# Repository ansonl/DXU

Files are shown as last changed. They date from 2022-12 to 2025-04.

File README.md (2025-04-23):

# DXU - Dual Extrusion Upgrade for Ultimaker Original+ and Ultimaker 2+

## Table of Contents

- ### [Marlin 2 firmware, calibration, and configuration instructions for DXUv2](https://github.com/ansonl/DXU/blob/master/Firmware/README.md) 

- ### [DXUv2 3D printable files](https://github.com/ansonl/DXU/tree/master/AL-DXUv2)

  - DXUv2 reuses the stock Ultimaker printhead metal parts for a more compact and durable printhead.

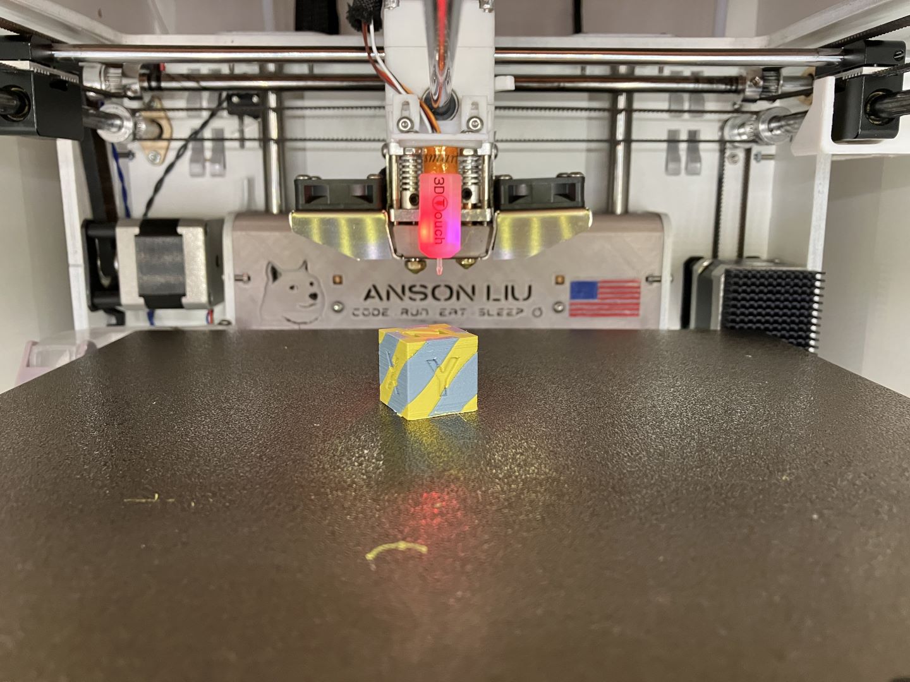
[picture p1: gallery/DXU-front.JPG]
DXU front


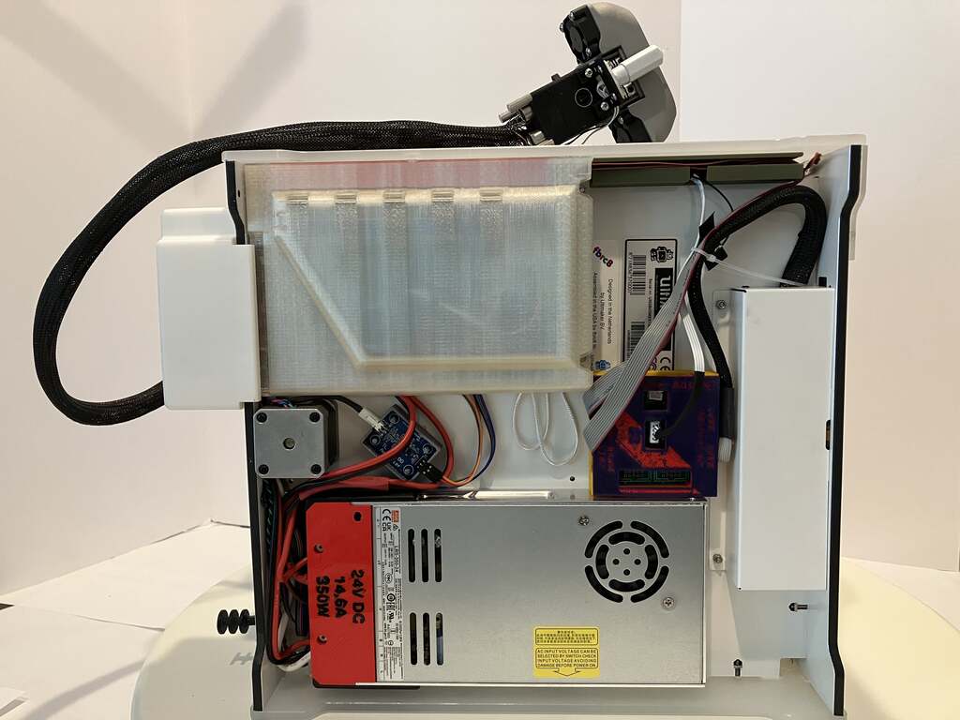
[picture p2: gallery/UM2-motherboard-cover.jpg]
DXUv2 bottom


### Improved/Updated DXU resources are in the `AL-*` folders. 

## DXUv2

1. See [post1](https://community.ultimaker.com/topic/24553-dxu-efficient-dual-extrusion-upgrade-for-um2/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) and [post2](https://community.ultimaker.com/topic/24553-dxu-efficient-dual-extrusion-upgrade-for-um2/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) for DXUv2 info
1. Make all the parts in `AL-DXUv2/master parts to print/` out of high temperature plastic like SLS Nylon.
1. Make the 3 hotend holder models in `AL-DXUv2/prototyping parts/DXUv2-hotend-holder` out of aluminum. You can machine it out of the existing Ultimaker part or get it SLM printed in aluminum. I did both and the SLM printed part from UnionFab is much more precise. Have the factory use my specification PDF for the threading depths and locations. This is save you a lot of crying and pain trying to thread blind holes yourself.

## Original DXU

1. [Marlin 2 firmware for DXU](https://github.com/ansonl/Marlin-DXU)
2. Dock adapted for UMO+ frame
3. Heater clamps with 1mm thin jaws. The linked Taobao seller sells a quality all metal hotend but the heatsink flanges are only 1mm vs 2mm apart. The seller says he can do a special order of heatsinks with 2mm flange spacing with a minimum order quantity of 50. 
4. Cura profile with calibration and improvements for DXU UMO+ are merged into Cura. 
5. Input Shaping calibration gcode and presets.

## Cura profile notes

I have not had time to update all the downloadable Cura profiles with the [better adaptive start/end gcode](https://ansonliu.com/2024/10/cura-adaptive-dual-extruder-start-gcode/) located in `AL-DXUv2/start-end-gcode`. Please copy and paste them into your Cura printer settings to use them.

### DISCUSSION:
https://community.ultimaker.com/topic/24553-dxu-another-dual-extrusion-upgrade-for-um2/

### CREDITS:

##### DXU:  
Original DXU by yyh1002

DXU variant by benleo888
##### Hardware:  
Lever action is inspired by Ultimaker 3.   
##### Firmware:   
Marlin 2 firmware

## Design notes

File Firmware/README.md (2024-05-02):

## Marlin 2 Configurations
Configurations for UMO+, UM2, UM2+ merged upstream to MarlinFirmware/Configurations are available at: [MarlinFirmware/Configurations](https://github.com/MarlinFirmware/Configurations/tree/bugfix-2.1.x/config/examples/Ultimaker)

These configurations are automatically merged with Configuration file version updates so accuracy is not guaranteed. All configurations can be used on single extruder printers by changing the extruder count from 2 to 1 and commenting out the multi extruder, thermistor, and extruder defines.

### PID Values Calibration

Determine your own PID by running [M303](https://marlinfw.org/docs/gcode/M303.html) or use the below values as reference.

#### Hotend PID values using 35 W heater cartridge

| Printhead | PID values in Gcode. Save to EEPROM with `M500` |
| --- | --- |
| Stock UM2+ | `M301 P8.86 I0.68 D28.86` |
| DXU PTFE with PI spacer | `M301 P13.95 I1.77 D27.42` |
| DXU all-metal | `M301 P10.85 I1.08 D27.33` |
| DXUv2 non-lifting nozzle (left) | `M301 E0 P15.15 I1.78 D32.26` |
| DXUv2 lifting nozzle (left) | `M301 E1 P15.53 I1.79 D33.71` |

#### Heated bed PID values using Ultimaker 120 W heated bed

| Printhead | PID values in Gcode. Save to EEPROM with `M500` |
| --- | --- |
| Stock UM glass bed | `M304 P124.55 I23.46 D165.29` |
| Textured PEI on magnetic metal sheet | `M304 D372.47 I14.05 P88.61` |

### EStep (steps/mm) Calibration

Determine your extruder steps/mm to avoid over/under extrusion. Even stock and clone extruders have variances that deviate from default steps/mm values!

| Extruder | steps/mm with 1.8°/step (UMO+/UM2+ extruder motor) | steps/mm with 0.9°/step (UM2 extruder motor) |
| --- | --- | --- |
| UM2+ Extruder | `M92 E369` | `M92 E738` |
| UM2+ Extruder (aliexpress) | `M92 E357` - `M92 E360` | `M92 E715` - `M92 E720` |

1. Disconnect bowden tube and printhead from extruder. 
2. Disable Cold Extrude protection. `M302 P1`
3. Set current extruder position in software to 0. `G92 E0`
4. Feed filament into extruder. Mark the location on the filament that sticks out from the extruder filament output hole using a sharpie. 
5. Move 100 mm of filament forward. `G0 E100 F100`
6. Mark location of filament that sticks out from the extruder filament output hole.
7. Measure distance between markings to determine actual distance of filament moved forward.
8. Calculate correct steps/mm manually or `corrected esteps = current esteps * (actual distance in mm)/100mm` or use [TH3D EStep Calculator](https://www.th3dstudio.com/estep-calculator/)
9. Set new steps/mm `M92 E<esteps>` e.g. `M92 E369`.
10. Return to step 3 and verify 100m of filament is actually moved.

### Hotend Offset Calibration

Stock hotend offset values for the second extruder are `M218 T1 X18 Y0 Z-2`
Stock probe offset values are `NOZZLE_TO_PROBE_OFFSET { 9, -19.5, -1 }`

#### Hotend Offset X/Y Calibration

1. Print dual X/Y calibration print [here](https://www.thingiverse.com/thing:1741265) or in the `AL-Hotend Calibration folder`.
2. Compare print results and set hotend offsets with [`M218`](https://marlinfw.org/docs/gcode/M218.html). `M218 T1 XNNN YNNN`

#### Hotend Offset Z Calibration

1. Switch to first extruder. `T0`
2. Home Z axis. Optionally home X/Y axis and move printhead to center of X/Y. `G28` `G0 X100 Y100`
3. Move Z axis to `0` position where nozzle touches or is ~0.1 mm above the bed for the paper calibration method. Using a piece of paper/gauge sliding between nozzle and bed, note the physical distance (not the value on the screen) between the nozzle and bed at Z0. `G0 Z0`
4. Move Z axis down at least `5 mm` to make space for the second extruder. `G0 Z5`
5. Manually activate second extruder with your hand or a tool. Do not activate with toolchange gcode `T1` unless the `HOTEND_OFFSET_Z` for the second extruder is set to `0`.
6. Move Z axis up until the physical distance between the second nozzle and bed are the same as the physical distance between the first nozzle and bed that you remembered earlier. Use a paper/gauge to get the right distance. Use the negative values of the Z position reported by the printer software as the `HOTEND_OFFSET_Z` for the second extruder. E.g. If the reported Z position is 2.5 mm, use -2.5 mm. 
7. Set new hotend Z offset with `M218`. `M218 T1 ZNNNN`

### Toolchange G-code

The movement commands to switch between the extruders can be set in firmware or the slicer. I recommend setting this in firmware rather than in the slicer. This way the toolchange action and offset compensation is completely handled by firmware and you do not need to remember to set up the special movements and offsets in every slicer you use (if the slicer even has support for it). When the toolchange is set in the firmware, all that is needed to change a tool is calling `TXX` where `XX` is the new extruder index starting from `0`. 

Configuration macros to change in Marlin are `EVENT_GCODE_TOOLCHANGE_T0` and `EVENT_GCODE_TOOLCHANGE_T1`. All movements are based off of hotend 0's offset which should be `0,0,0`. Otherwise there would be no way to know which hotend offset is being switched from if there are more than 2 hotends. Marlin will translate the movement by the current hotend offset. 

| Printer Case | Extruder | Toolchange G-code |
| --- | --- | --- |
| UM2/UM2+ | `T0` | `G90\nG0 X214 F7200\nG0 Y178\nG0 X219 F1800\nG0 Y194.5\nG0 X214\nG0 Y169 F7200` |
| UM2/UM2+ | `T1` | `G90\nG0 X214 F7200\nG0 Y209\nG0 X220 F1800\nG0 Y193\nG0 X214\nG0 Y169 F7200` |
| UMO+ | `T0` | `G90\nG0 X211 F7200\nG0 Y167\nG0 X217 F1800\nG0 Y182\nG0 X211\nG0 Y166 F7200` |
| UMO+ | `T1` | `G90\nG0 X211 F7200\nG0 Y198\nG0 X219 F1800\nG0 Y181\nG0 X211\nG0 Y166 F7200` |

### Save Printer Settings

Save settings to persistent storage on board the printer EEPROM with `M500`

## Marlin 2 Firmware 
Firmware source code customized for 3D printers

| Machine style | Motherboard (controller board) | Firmware source code branch |
| --- | --- | --- |
| UMO+/UM2/UM2+ w/ DXU | `ULTIMAINBOARD` | [ansonl/Marlin:dxu-ultimaker-ultimainboard-2](https://github.com/ansonl/Marlin/tree/dxu-ultimaker-ultimainboard-2) |
| UMO+/UM2/UM2+ w/ DXU | `BTT_OCTOPUS_PRO_V1_0` | [ansonl/Marlin:dxu-ultimaker-btt-octopus-pro-1](https://github.com/ansonl/Marlin/tree/dxu-ultimaker-btt-octopus-pro-1) |

*If you have a modified Marlin 2 firmware that you would like to add to this list, please add it in a PR.*

### Firmware notes for each branch versus *MarlinFirmware/Marlin* upstream 

#### ansonl/Marlin:dxu-ultimaker-ultimainboard-2
- https://github.com/MarlinFirmware/Marlin/issues/25117 - Marlin 2.1.2 Input Shaping may skip steps on AVR at high speeds > 250mm/s.

#### ansonl/Marlin:dxu-ultimaker-btt-octopus-pro-1
- Pins changes
  - `pins_BTT_OCTOPUS_PRO_V1_0.h`
  - `pins_BTT_OCTOPUS_V1_common.h`
- https://github.com/MarlinFirmware/Marlin/pull/25683 - OTA Firmware update via SDIO card update

### Merged to upstream
- https://github.com/MarlinFirmware/Marlin/pull/23466
- https://github.com/MarlinFirmware/Marlin/pull/24553
- https://github.com/MarlinFirmware/Marlin/pull/24797
- https://github.com/MarlinFirmware/Marlin/pull/25399
- https://github.com/MarlinFirmware/Marlin/pull/25707

## Cura printer settings

```json
"overrides":
    {
        "line_width": { "value": "machine_nozzle_size" },
        "machine_depth": { "default_value": 216 },
        "machine_disallowed_areas":
        {
            "default_value": [
                [
                    [100, -102.5],
                    [110, -102.5],
                    [110, -62.5],
                    [100, -62.5]
                ]
            ]
        },
        "machine_end_gcode": { "value": "\"\"  if machine_gcode_flavor == \"UltiGCode\" else \"G91 ;Relative movement\\nG0 X-8.0 Y-8.0 Z3.5 E-4.5 F18000 ;Wiping+material retraction ;increase bed lower 0.5>5.0 and add Y movement\\nG0 F10000 Z1.5 E4.5 ;Compensation for the retraction\\nG90 ;Disable relative movement\\nM400 ;wait for all moves in planner to complete\\nG90 ;absolute positioning\\nM104 S0 T0 ;extruder heater off\\nM104 S0 T1\\nM140 S0 ;turn off bed\\nT0 ; move to the first head\\nG27; park toolhead\\nM107 ;fan off\\nM355 S0;turn off case light\"" },
        "machine_extruder_count": { "default_value": 1 },
        "machine_gcode_flavor": { "default_value": "RepRap (Marlin/Sprinter)" },
        "machine_head_with_fans_polygon":
        {
            "default_value": [
                [-46, 30],
                [-46, -34],
                [66, 30],
                [66, -34]
            ]
        },
        "machine_heat_zone_length": { "default_value": 20 },
        "machine_heated_bed": { "default_value": true },
        "machine_height": { "default_value": 208 },
        "machine_max_feedrate_x": { "default_value": 300 },
        "machine_max_feedrate_y": { "default_value": 300 },
        "machine_max_feedrate_z": { "default_value": 40 },
        "machine_min_cool_heat_time_window": { "default_value": 15.0 },
        "machine_name": { "default_value": "dxu2" },
        "machine_nozzle_cool_down_speed": { "default_value": 0.8 },
        "machine_nozzle_expansion_angle": { "default_value": 45 },
        "machine_nozzle_head_distance": { "default_value": 3 },
        "machine_nozzle_heat_up_speed": { "default_value": 1.4 },
        "machine_nozzle_size": { "default_value": 0.4 },
        "machine_start_gcode": { "value": "\"\"  if machine_gcode_flavor == \"UltiGCode\" else \"; DXUv2 improved start priming Gcode for dual nozzles for single material print by ansonl\\nM355 S1 P25 ; Turn on case light dim\\nM190 S{material_bed_temperature_layer_0}\\nG28 ; Home all\\nG29 ; Run automatic bed leveling. Comment this line out if auto bed leveling is not desired.\\nM104 T0 S{material_standby_temperature, 0} ; Preheat T0 to standby temp\\nG21 ; Metric values\\nG90 ; Absolute positioning\\nM82 ; Set extruder to absolute mode\\nM107 ; Start with the fan off\\nM200 D0 T{initial_extruder_nr} ; Reset filament diameter\\nG0 X200 F7200 ; move to safe X and Y location from right side after ending ABL homing\\nG1 Y150 F7200\\nM104 T{initial_extruder_nr} S{material_print_temperature_layer_0, initial_extruder_nr}\\nT{initial_extruder_nr} ;switch to the first nozzle used for print\\nM400 ;finish all moves\\nG0 Z20 F2400\\nG0 X214 F18000\\nG0 Y2 F18000\\nM109 T{initial_extruder_nr} S{material_print_temperature_layer_0, initial_extruder_nr}\\n;Final wipe sequence for initial extruder\\nG0 X212 Z0.3 F600\\nG92 E05\\nG1 Y45 E6.5 F1000\\nG92 E0\\nG1 E-0.5 F1500 ; retract\\nG92 E0\\nG1 Y100 F18000\\n;end of startup sequence\\n\\nM355 S1 P50;turn on case light\"" },
        "machine_use_extruder_offset_to_offset_coords": { "default_value": false },
        "machine_width": { "default_value": 221 },
        "material_adhesion_tendency": { "enabled": true },
        "material_diameter": { "default_value": 1.75 },
        "prime_tower_position_x": { "value": "180" },
        "prime_tower_position_y": { "value": "160" },
        "retraction_amount": { "default_value": 3 },
        "retraction_min_travel": { "value": "line_width * 2" },
        "retraction_speed": { "default_value": 25 },
        "switch_extruder_prime_speed": { "value": "retraction_prime_speed" },
        "switch_extruder_retraction_amount": { "value": "retraction_amount" },
        "switch_extruder_retraction_speed": { "value": "retraction_retract_speed" },
        "switch_extruder_retraction_speeds": { "value": "retraction_speed" },
        "travel_avoid_distance": { "value": "3 if extruders_enabled_count > 1 else machine_nozzle_tip_outer_diameter / 2 * 1.5" }
    }
  ```

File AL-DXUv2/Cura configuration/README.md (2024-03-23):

# Cura Profile Installation

1. Download the latest Cura profile `*.zip` file in this directory.
2. Unzip the archive keeping the files within the respective `definitions`, `extruders`, `variants` folders.
3. Move the folders to the Cura configuration directory `%HOME%/AppData/Roaming/cura/XXX/` where `XXX` is the Cura version number. This will merge the unzipped folders' contents with the existing Cura profile folders' contents.
4. Close and restart Cura.
5. Add the DXUv2 printer as a non-networked printer. DXUv2 printers will be listed under the DXU category.

## Retraction Settings

My optimal retraction settings to use as a starting point. Increasing the nozzle switch retraction distance ensures that no oozing occurs from the inactive extruder. 

| Setting | Value |
| --- | --- |
| Retraction Distance | 2.4 mm |
| Retraction Speed | 25 mm/s |
| Nozzle Switch Retraction Distance | 16 mm |
| Nozzle Switch Retraction Speed | 20 mm/s |

## Start Gcode

Optimized start gcode that properly primes both extruders **regardless of previous nozzle switch retraction state**. The final prime wipes on a previous prime line that helps clear the nozzle of any oozing. 

```
; Octolapse variables
; Script based on an original created by tjjfvi (https://github.com/tjjfvi)
; An up-to-date version of the tjjfvi's original script can be found
; here:  https://csi.t6.fyi/
; Note - This script will only work in Cura V4.2 and above!
; --- Global Settings
; layer_height = {layer_height}
; smooth_spiralized_contours = {smooth_spiralized_contours}
; magic_mesh_surface_mode = {magic_mesh_surface_mode}
; machine_extruder_count = {machine_extruder_count}
; --- Single Extruder Settings
; speed_z_hop = {speed_z_hop}
; retraction_amount = {retraction_amount}
; retraction_hop = {retraction_hop}
; retraction_hop_enabled = {retraction_hop_enabled}
; retraction_enable = {retraction_enable}
; retraction_speed = {retraction_speed}
; retraction_retract_speed = {retraction_retract_speed}
; retraction_prime_speed = {retraction_prime_speed}
; speed_travel = {speed_travel}
; --- Multi-Extruder Settings
; speed_z_hop_0 = {speed_z_hop, 0}
; speed_z_hop_1 = {speed_z_hop, 1}
; retraction_amount_0 = {retraction_amount, 0}
; retraction_amount_1 = {retraction_amount, 1}
; retraction_hop_0 = {retraction_hop, 0}
; retraction_hop_1 = {retraction_hop, 1}
; retraction_hop_enabled_0 = {retraction_hop_enabled, 0}
; retraction_hop_enabled_1 = {retraction_hop_enabled, 1}
; retraction_prime_speed_0 = {retraction_prime_speed, 0}
; retraction_prime_speed_1 = {retraction_prime_speed, 1}
; retraction_retract_speed_0 = {retraction_retract_speed, 0}
; retraction_retract_speed_1 = {retraction_retract_speed, 1}
; retraction_speed_0 = {retraction_speed, 0}
; retraction_speed_1 = {retraction_speed, 1}
; retraction_enable_0 = {retraction_enable, 0}
; retraction_enable_1 = {retraction_enable, 1}
; speed_travel_0 = {speed_travel, 0}
; speed_travel_1 = {speed_travel, 1}
; material_bed_temperature={material_bed_temperature}
; material_print_temperature={material_print_temperature}
; material_print_temperature_layer_0={material_print_temperature_layer_0}
; switch_extruder_retraction_amount_0={switch_extruder_retraction_amount, 0}
; switch_extruder_retraction_amount_1={switch_extruder_retraction_amount, 1}

; DXUv2 improved start priming Gcode for dual nozzles for multi-material print
M355 S1 P25 ; Turn on case light dim
M190 S{material_bed_temperature_layer_0}
G28 ; Home all
;M420 S1 ; Enable and load bed mesh
G29 ; Run automatic bed leveling. Comment this line out if auto bed leveling is not desired.
M104 T0 S{material_standby_temperature, 0} ; Preheat T0 to standby temp
M104 T1 S{material_standby_temperature, 1} ; Preheat T1 to standby temp
G21 ; Metric values
G90 ; Absolute positioning
M82 ; Set extruder to absolute mode
M107 ; Start with the fan off
M200 D0 T0 ; Reset filament diameter
M200 D0 T1 ; Reset filament diameter
G0 X200 F7200 ; Move to safe X and Y location from right side after ending ABL homing. Move X before Y to avoid hitting switching lever.
G1 Y150 F7200
; Prime routine for T1 in normally 
T1 ; move to the nozzle 2
M104 T1 S{material_final_print_temperature, 1} ; Start heating up T1
G0 Z10 F2400 ; move the platform down to 10mm
M109 T1 S{material_print_temperature, 1} ; Heat up and wait for T1
G0 Y150 F7200 ; Move printhead to safe Y location to move right.
G0 X50 Y1 F7200 ; Add HOTEND_OFFSET_Y[1] to Y0 (or forward-most safe Y location when T1 is active) to get Gcode Y parameter
G0 X95 Z0.3 F2400 ; lower nozzle
G92 E0 ; reset E location
G1 X225 Y1 Z0.3 E{switch_extruder_retraction_amount, 1} F1500 ; Add HOTEND_OFFSET_X[1] to X217 (or right-most safe X location when T1 is active) to get actual Gcode X parameter.
G3 X235 Y11 I0 J10 F7200
G0 X235 Y11 Z0.3 F7200
M104 T1 S{material_final_print_temperature, 1} ; Start cooling down nozzle to reduce oozing
G92 E0
G1 Y70 E3 F1000 ; intro line
M104 T1 S{material_standby_temperature, 1}
G92 E0 
G1 E-{switch_extruder_retraction_amount, 1} F1200 ; retract
G0 Y105 F18000 ; break line
G0 Y150 Z10 F2400 ; raise nozzle
; Prime routine for T0
T0 ; move to the nozzle 1
M104 T0 S{material_final_print_temperature, 0} ; Start heating up T0
G0 Z10 F2400
M109 T0 S{material_print_temperature, 0}
G0 Y150 F7200 ; Move printhead to safe Y location to move right.
G0 X32 Y3 F7200
G0 X77 Z0.3 F2400
G92 E0 ; reset E location
G1 X207 Y3 Z0.3 E{switch_extruder_retraction_amount, 0} F1500
G3 X217 Y13 I0 J10 F7200
G0 X217 Y13 Z0.3 F7200
M104 T0 S{material_final_print_temperature, 0} ; Start cooling down nozzle to reduce oozing
G92 E0 ; reset E location
G1 Y72 E3 F1000 ; intro line
M104 T0 S{material_standby_temperature, 0}
M104 T{initial_extruder_nr} S{material_print_temperature, initial_extruder_nr} ; Start heating initial nozzle. Do not wait.
G92 E0
G1 E-{switch_extruder_retraction_amount, 0} F1200 ; retract
G0 Y105 F18000 ; break line
G0 Y150 Z10 F2400 ; raise nozzle
; Final prime and wipe sequence for initial extruder (usually T0)
T{initial_extruder_nr} ; move to the initial nozzle used for print
M400 ;finish all moves
G0 Z20 F2400
G0 X212 F7200
G0 Y70 F7200
M109 T{initial_extruder_nr} S{material_print_temperature, initial_extruder_nr} ; Wait for initial nozzle to reach temp
G92 E0
G1 E{switch_extruder_retraction_amount, initial_extruder_nr} F1200 ; prime by switching length
G0 X217 Y50 Z0.5 F7200
G92 E0
G0 Y9.4 Z0.5 E3 F7200
G2 X212 Y3.4 Z0.4 I-6 J0 F7200
M104 T{initial_extruder_nr} S{material_print_temperature_layer_0, initial_extruder_nr} ; Start heating to first layer temp
G0 X207 Y3.4 Z0.4 F7200
G2 X205 Y5.4 Z0.3 I0 J2 F7200
G0 X205 Y5.4 Z0.3 F7200
G1 Y10 F18000 ; break line
G92 E0
G1 Y50 E2 F1000 ; extrude line
G92 E0
G1 E-0.5 F1500 ; retract slightly
G1 Y100 F18000 ; break line
G92 E0
M355 S1 P255; Turn on case light brighter
;end of startup sequence
```

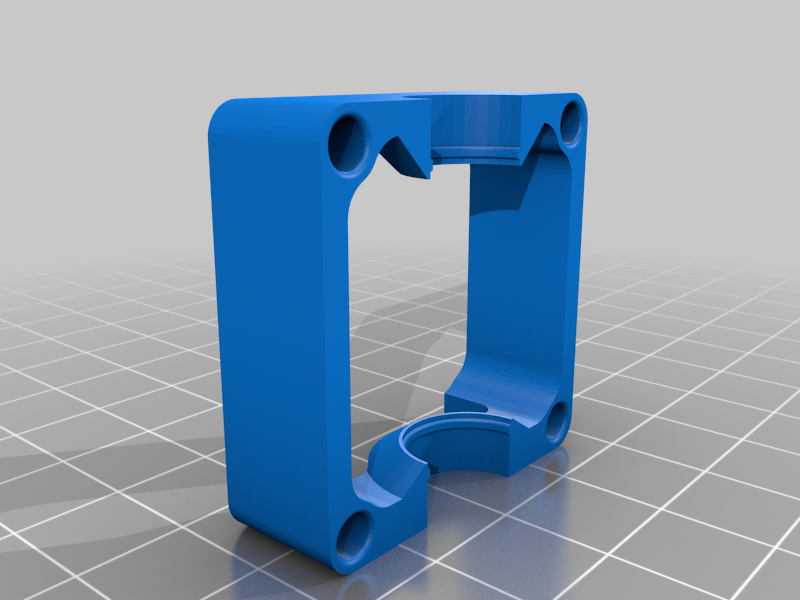
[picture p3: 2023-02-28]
AL-DXUv2/original community files/Special_mod_for_UM2_DXU_4655216/images/head_bottom.png

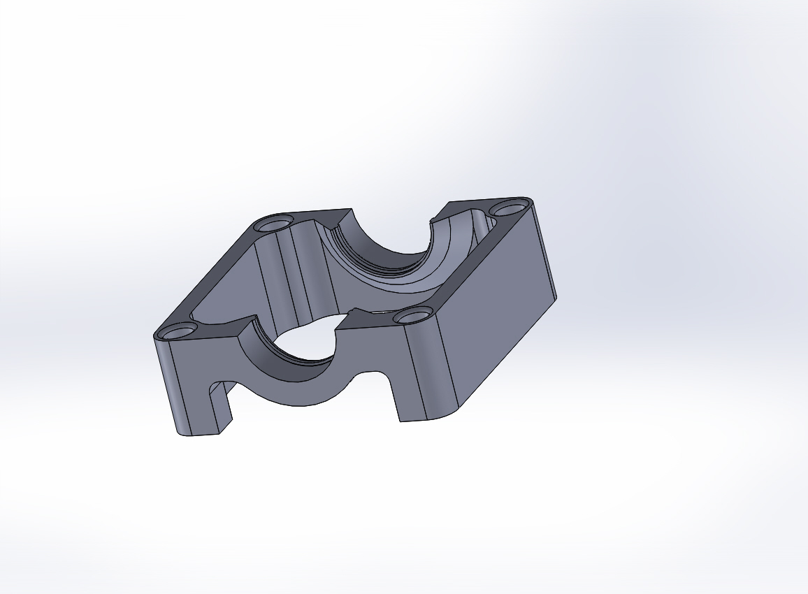
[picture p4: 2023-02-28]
AL-DXUv2/original community files/Special_mod_for_UM2_DXU_4655216/images/head_bottom.JPG

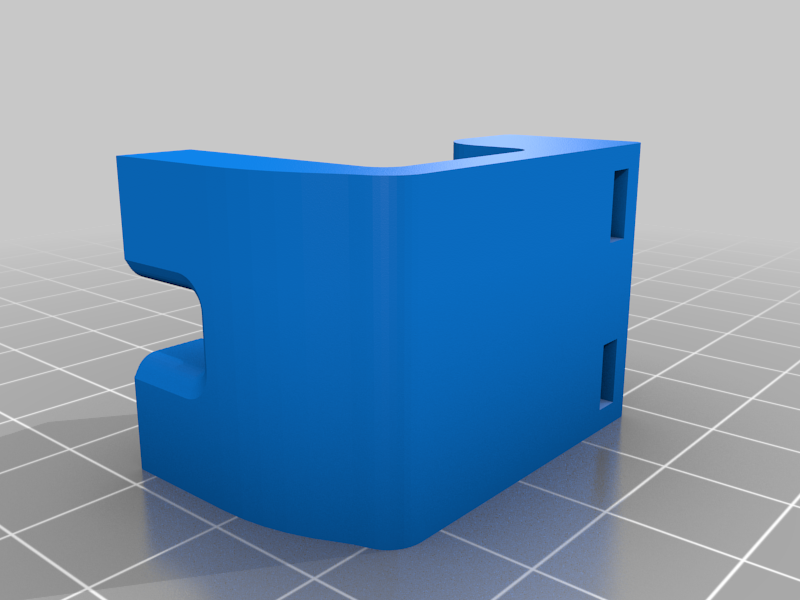
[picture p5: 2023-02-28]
AL-DXUv2/original community files/Special_mod_for_UM2_DXU_4655216/images/base1.png

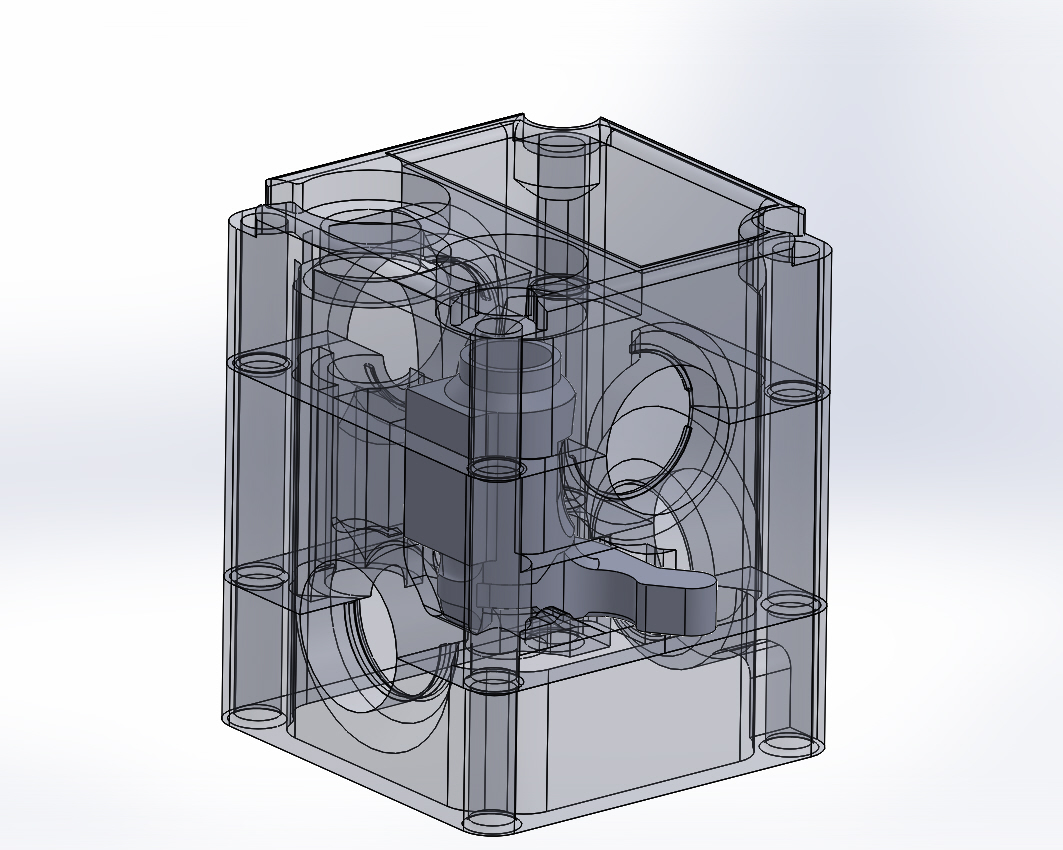
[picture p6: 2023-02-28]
AL-DXUv2/original community files/Special_mod_for_UM2_DXU_4655216/images/Assem1_3.JPG

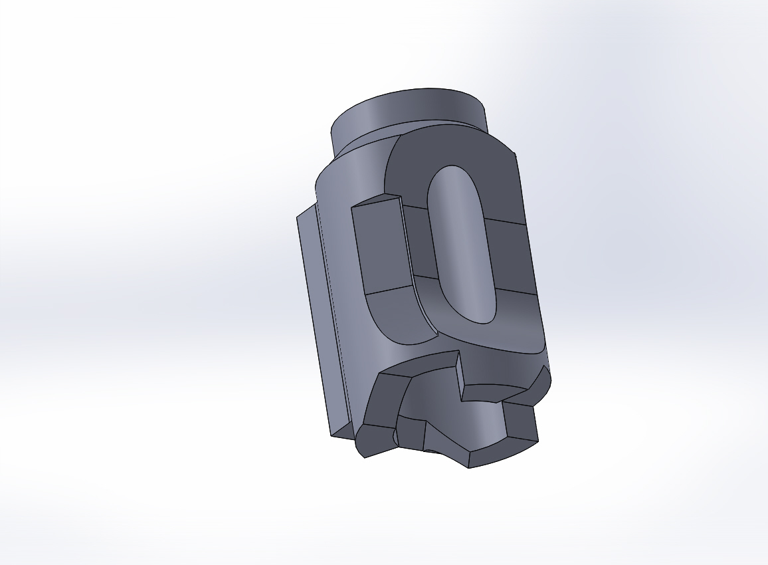
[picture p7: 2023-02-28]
AL-DXUv2/original community files/Special_mod_for_UM2_DXU_4655216/images/lever2.JPG

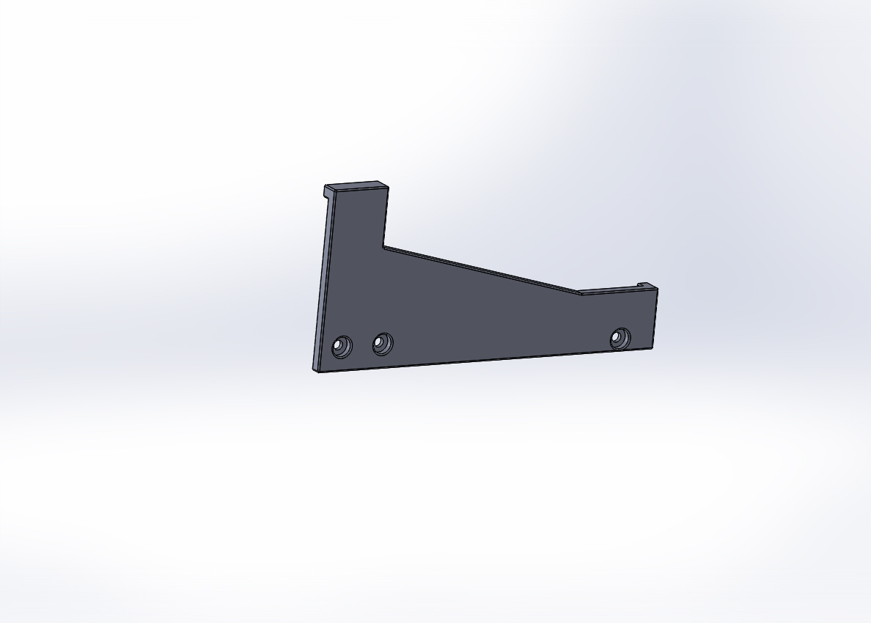
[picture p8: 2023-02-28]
AL-DXUv2/original community files/Special_mod_for_UM2_DXU_4655216/images/base2.JPG

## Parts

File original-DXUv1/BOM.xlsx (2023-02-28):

Bill of Material 物料清单
物品/Material |  | 数量/Quantity | 链接/Link | 选项/Option | 备用链接/Alternative Link
胖子UM2 1.75热端新直通套件 | UM2 1.75 Hotend Kit (Heatsink, Bowden Coupler) | 2 | https://item.taobao.com/item.htm?spm=a1z10.5-c.w4002-9918354853.34.576d75aec3Kk6M&id=521401997290 | 新直通套件 | https://www.aliexpress.com/store/product/3D-Printer-Upgrade-Ultimaker-2-UM2-Extended-Newest-Olsson-Block-Nozzle-Hot-end-Kit/1877169_32988128287.html
胖子UM2 1.75热端新直通加热块 | UM2 1.75 Hotend Heat Block | 2 | https://item.taobao.com/item.htm?spm=a1z10.5-c.w4002-9918354853.34.576d75aec3Kk6M&id=521401997290 | 新直通加热块
290度高温打印PI喉管垫片 2*4*1 | 290°C High Temp Print Hotend Insulator 2*4*1 | 2 | https://item.taobao.com/item.htm?spm=a1z10.5-c.w4002-9918354853.25.60724c2fxu3tfa&id=581596714621 | 小2*4*1
UM2加热棒 | UM2 Heater Cartridge | 2 | https://www.makerpoint.nl/nl/ultimaker-heater-cartridge-24v-35w-um2um2ext.html
UM2 PT100测温 | UM2 PT100 Sensor | 2 | https://www.makerpoint.nl/nl/ultimaker-pt100-b-sensor-glassfiber-um2um2ext.html
2*6.35四氟远程送料管 | 2*6.35 PTFE Bowden Tube | 2 | https://item.taobao.com/item.htm?spm=a1z10.5-c.w4002-9918354853.32.576d75aec3Kk6M&id=521852878986 | 2*6.35
6.35料管蓝白卡扣 | 6.35 Bowden Coupler | 2 | https://www.makerpoint.nl/nl/ultimaker-bowden-tube-clips-pack-ultimaker.html
1.75耗材挤出机 | 1.75 Filament Feeder | 2 | https://www.thingiverse.com/thing:2289203 | Use 2.85 version for 6.35 tube
NEMA17 42*48挤出机电机 | NEMA17 42*48 Stepper Motor | 1 | https://www.makerpoint.nl/nl/ultimaker-feeder-motor-um3-extended-assembly.html
3510 12v涡轮吹料风扇 | 3510 12v Blower Fan | 2 | https://au.mouser.com/ProductDetail/?qs=%2FW4LtXOBxKsfL3eA88psUg== |  | https://item.taobao.com/item.htm?id=538704495777&_u=t2dmg8j26111&qq-pf-to=pcqq.group
3010 5v热端散热风扇 | 3010 5v Hotend Cooling Fan | 1 | https://www.aliexpress.com/item/DC-Cooling-Fan-3010-Fan-30-30-10mm-3010-fans-5V-12V-24V-Suitable-for-extruders/32909524999.html | 3010-5v
直线轴承LM6LUU 6*12*35mm | Linear Bearing LM6LUU 6*12*35mm | 2 | https://sg.misumi-ec.com/vona2/detail/110302578040/
压缩弹簧 0.8*9*15 或近似（建议买几个不同粗细的） | Compression Spring 0.8*9*15 or similar | 1
M3*6平头螺丝 | M3*6 Countersunk Screw | 4 | https://www.mcmaster.com/92125A126
M3*16半圆头螺丝 | M3*16 Button Head Screw | 6 | https://www.mcmaster.com/92095A184
M3*20半圆头螺丝 | M3*20 Button Head Screw | 2 | https://www.mcmaster.com/92095A185
M3*35半圆头螺丝 | M3*35 Button Head Screw | 4 | https://www.mcmaster.com/92095A201
M3螺母 | M3 Nut | 8 | https://www.mcmaster.com/90592A085
M3*3顶丝 | M3*3 Set Screw Cup Head | 1 | https://www.mcmaster.com/91390A097

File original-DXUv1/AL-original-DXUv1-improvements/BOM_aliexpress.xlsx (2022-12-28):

Bill of Material 物料清单 |  | aliexpress
 |  | superbuy
物品/Material |  | digikey | 数量/Quantity | 链接/Link | 选项/Option | 备用链接/Alternative Link | price total
 | cost
胖子UM2 1.75热端新直通套件 | $14.00 | UM2 1.75 Hotend Kit (Heatsink, Bowden Coupler) | 2 | https://item.taobao.com/item.htm?spm=a1z10.5-c.w4002-9918354853.34.576d75aec3Kk6M&id=521401997290 | 新直通套件 | https://www.aliexpress.com/store/product/3D-Printer-Upgrade-Ultimaker-2-UM2-Extended-Newest-Olsson-Block-Nozzle-Hot-end-Kit/1877169_32988128287.html
胖子UM2 1.75热端新直通加热块 | $7.40 | UM2 1.75 Hotend Heat Block | 2 | https://item.taobao.com/item.htm?spm=a1z10.5-c.w4002-9918354853.34.576d75aec3Kk6M&id=521401997290 | 新直通加热块 | https://www.aliexpress.com/store/product/3D-Printer-Upgrade-Ultimaker-2-UM2-Extended-Newest-Olsson-Block-Nozzle-Hot-end-Kit/1877169_32988128287.html
290度高温打印PI喉管垫片 2*4*1 | $3.40 | 290°C High Temp Print Hotend Insulator 2*4*1 | 2 | https://item.taobao.com/item.htm?spm=a1z10.5-c.w4002-9918354853.25.60724c2fxu3tfa&id=581596714621 | 小2*4*1 | https://nl.aliexpress.com/item/4000192534992.html?spm=a2g0s.12269583.0.0.1e76454cuxyrYf
UM2加热棒 | $25.90 | UM2 Heater Cartridge | 2 | https://www.makerpoint.nl/nl/ultimaker-heater-cartridge-24v-35w-um2um2ext.html |  | https://nl.aliexpress.com/item/32810827757.html?scm_id=1007.13338.133222.0&scm-url=1007.13338.133222.0
UM2 PT100测温 | $12.00 | UM2 PT100 Sensor | 2 | https://www.makerpoint.nl/nl/ultimaker-pt100-b-sensor-glassfiber-um2um2ext.html |  | https://nl.aliexpress.com/item/32855410598.html?scm_id=1007.13339.146401.0&scm-url=1007.13339.146401.0
2*6.35四氟远程送料管 | $4.29 | 2*6.35 PTFE Bowden Tube | 2 | https://item.taobao.com/item.htm?spm=a1z10.5-c.w4002-9918354853.32.576d75aec3Kk6M&id=521852878986 | 2*6.35 | https://nl.aliexpress.com/item/32825558666.html?scm_id=1007.13339.146401.0&scm-url=1007.13339.146401.0
6.35料管蓝白卡扣 | $2.09 | 6.35 Bowden Coupler | 2 | https://www.makerpoint.nl/nl/ultimaker-bowden-tube-clips-pack-ultimaker.html |  | https://nl.aliexpress.com/item/32877302016.html
1.75耗材挤出机 | $19.90 | 1.75 Filament Feeder | 2 | https://www.thingiverse.com/thing:2289203 | Use 2.85 version for 6.35 tube | https://nl.aliexpress.com/item/32708317695.html?scm_id=1007.13338.148453.0&scm-url=1007.13338.148453.0
NEMA17 42*48挤出机电机 |  | NEMA17 42*48 Stepper Motor | 1 | https://www.makerpoint.nl/nl/ultimaker-feeder-motor-um3-extended-assembly.html |  | https://nl.aliexpress.com/item/32826534702.html?spm=a2g0z.12010615.8148356.2.2ff2e1062wfFfS
3510 12v涡轮吹料风扇 | $28.00 | 3510 12v Blower Fan OR 3015 12v | 2 | https://au.mouser.com/ProductDetail/?qs=%2FW4LtXOBxKsfL3eA88psUg== |  | https://item.taobao.com/item.htm?id=538704495777&_u=t2dmg8j26111&qq-pf-to=pcqq.group
3010 5v热端散热风扇 | $1.78 | 3010 5v Hotend Cooling Fan OR 2510 5v | 1 | https://www.aliexpress.com/item/DC-Cooling-Fan-3010-Fan-30-30-10mm-3010-fans-5V-12V-24V-Suitable-for-extruders/32909524999.html | 3010-5v
直线轴承LM6LUU 6*12*35mm | $3.16 | Linear Bearing LM6LUU 6*12*35mm | 2 | https://sg.misumi-ec.com/vona2/detail/110302578040/ |  | https://nl.aliexpress.com/item/32811509297.html?spm=a2g0s.9042311.0.0.38f14c4dQjH6Pd
压缩弹簧 0.8*9*15 或近似（建议买几个不同粗细的） | $5.36 | Compression Spring 0.8*9*15 or similar | 1 |  |  | https://nl.aliexpress.com/item/32981497125.html
M3*6平头螺丝 | $0.58 | M3*6 Countersunk Screw | 4 | https://www.mcmaster.com/92125A126 |  | https://nl.aliexpress.com/item/4000193155954.html?scm_id=1007.13339.146401.0&scm-url=1007.13339.146401.0
M3*16半圆头螺丝 | $2.11 | M3*16 Button Head Screw | 6 | https://www.mcmaster.com/92095A184 |  | https://nl.aliexpress.com/item/4000117933430.html
M3*20半圆头螺丝 | $2.47 | M3*20 Button Head Screw | 2 | https://www.mcmaster.com/92095A185 |  | https://nl.aliexpress.com/item/4000117933430.html
M3*35半圆头螺丝 | $3.67 | M3*35 Button Head Screw | 4 | https://www.mcmaster.com/92095A201 |  | https://nl.aliexpress.com/item/4000117933430.html
M3螺母 |  | M3 Nut | 8 | https://www.mcmaster.com/90592A085 |  | https://nl.aliexpress.com/item/4000170946467.html?scm_id=1007.13339.146401.0&scm-url=1007.13339.146401.0
M3*3顶丝 | $1.08 | M3*3 Set Screw Cup Head | 1 | https://www.mcmaster.com/91390A097 |  | https://nl.aliexpress.com/item/4000158332347.html?spm=a2g0s.9042311.0.0.38f14c4dQjH6Pd
m3 spacer | $1.66 | m3 spacer 7-8mm
KPXX-4P | $8.00 | r7b male connector (psu side) | 2 | https://www.digikey.com/en/products/detail/kycon-inc/KPPX-4P/9990085
KPJX-CM-4S | $7.00 | r7b female connector | 1
GST280A24-C6P | $120.00 | 280w power supply with c6p connector (replace with r7b) |  | https://www.onlinecomponents.com/en/mean-well/gst280a24c6p-48236195.html
 | $273.85

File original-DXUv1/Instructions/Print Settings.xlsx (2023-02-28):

Print Settings 打印设置
零件名称/Parts Name | 材料/Material | 层高/Layer Height | 外壁线数/Wall Line Count | 支撑/Support
01 Housing Front | PC or PA66 | 0.2 | 5 | NO
02 Housing Back
03 Fan Shroud 3510 |  |  |  | YES
04 Fan Cover 3010
11 Lever 1 |  | 0.1 | 5 | NO
12 Lever 2 |  |  |  | YES
13 Lever 3 |  |  |  | NO
21 Dock |  | 0.2 | 5 | NO
22 Dock liner | PLA |  |  | NO
31 Heater clamp a | PC or PA66 | 0.2 |  | NO
32 Heater clamp b
33 Hotend fan pusher

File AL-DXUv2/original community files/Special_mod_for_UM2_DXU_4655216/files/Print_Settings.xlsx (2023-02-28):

Print Settings
Parts Name | Material | Layer Height | Wall Line Count | Top/Bottom layer | Support | Speed
head_top | ABS | 0.1 | 5 | 8 | Yes | 40
head_mid_support |  |  |  |  | No
head_bottom_support
Lever1_support |  |  |  |  | No | 20
Lever2
springadapter
fan_shroud1 |  |  |  |  | Yes | 50
fan_shroud2 |  |  |  |  | No
base1 |  |  |  |  | No | 50
base2

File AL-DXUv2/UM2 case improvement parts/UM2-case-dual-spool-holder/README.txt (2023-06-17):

Ultimaker 3 Spool Holder by lendres on Thingiverse: https://www.thingiverse.com/thing:2564645

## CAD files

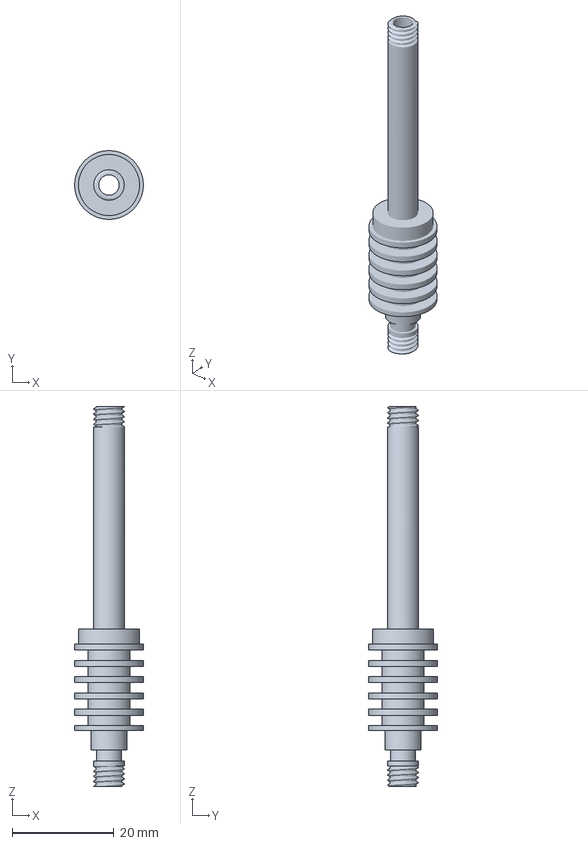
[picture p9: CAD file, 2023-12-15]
AL-DXUv2/prototyping parts/hotend-parts-pipe heatsink assembly w_ through hole.3mf
13.5 x 13.5 x 74.7 mm

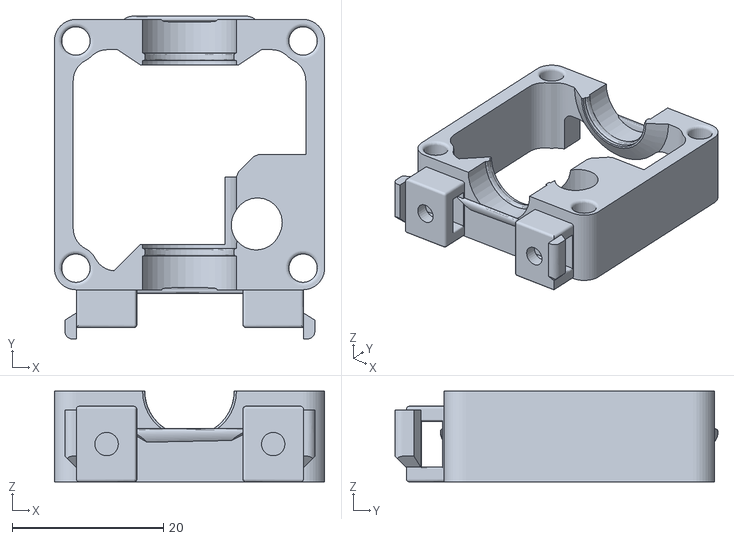
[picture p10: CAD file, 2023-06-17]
AL-DXUv2/master parts to print/head_bottom_bltouch_mount.stl
35.7 x 42.7 x 12.0

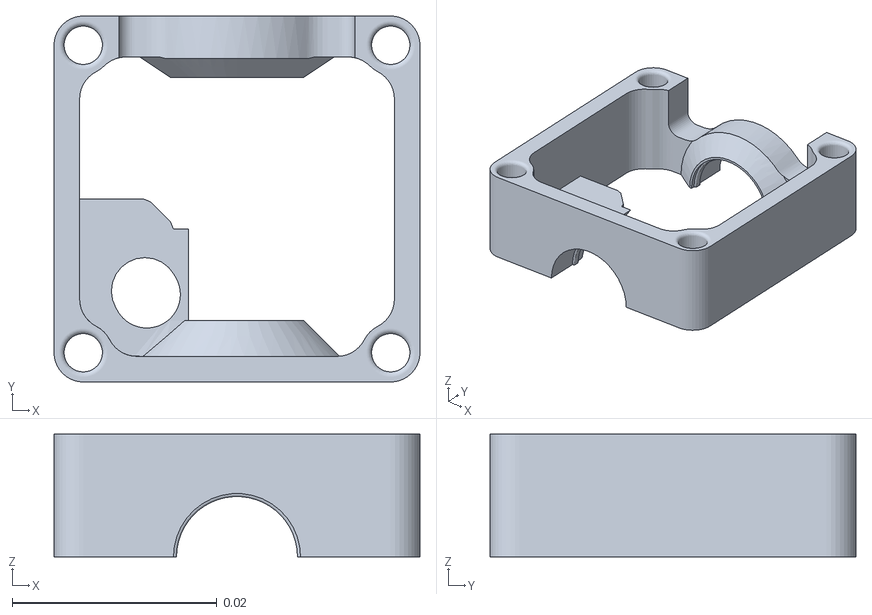
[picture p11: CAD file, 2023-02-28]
AL-DXUv2/original community files/head_bottom_repaired.stl
0.0357 x 0.0357 x 0.012

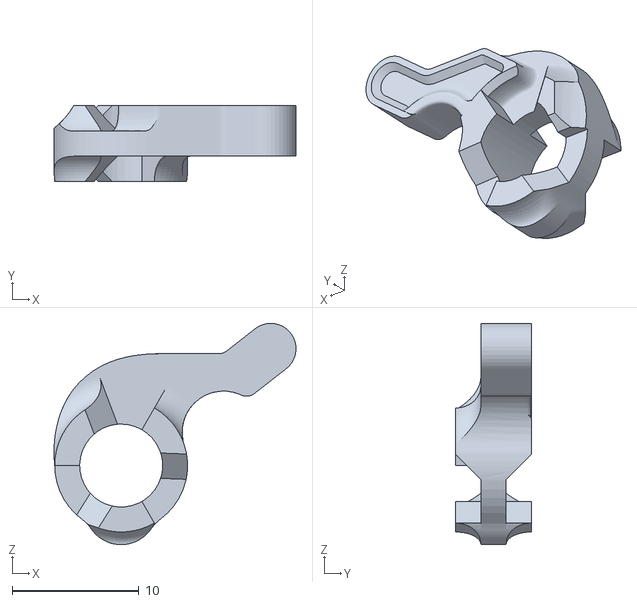
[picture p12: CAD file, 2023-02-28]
AL-DXUv2/original community files/Special_mod_for_UM2_DXU_4655216/files/lever1.STL
19.1 x 6.00 x 17.5

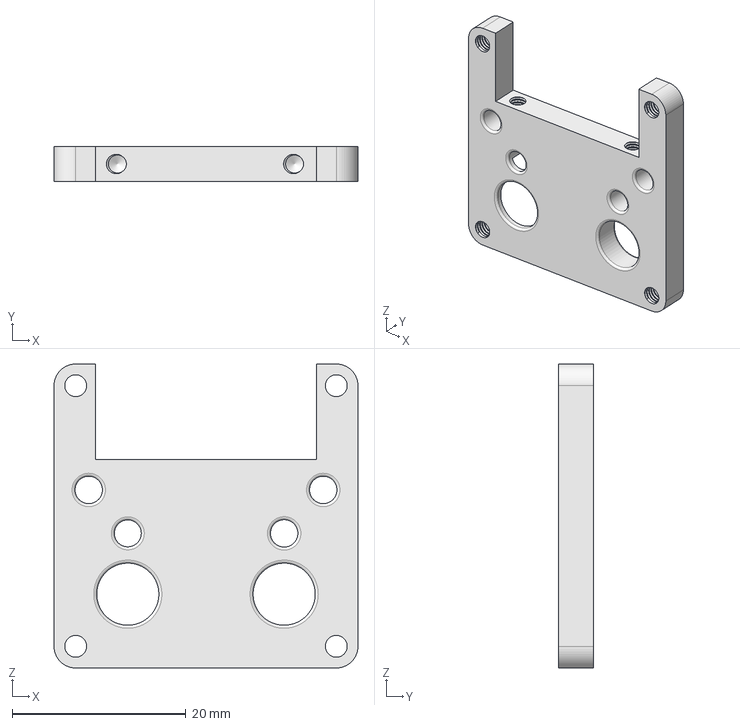
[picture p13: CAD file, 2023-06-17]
AL-DXUv2/prototyping parts/DXUv2-hotend-holder/printhead_mount-1306 bottom.step
35.0 x 4.00 x 35.0 mm

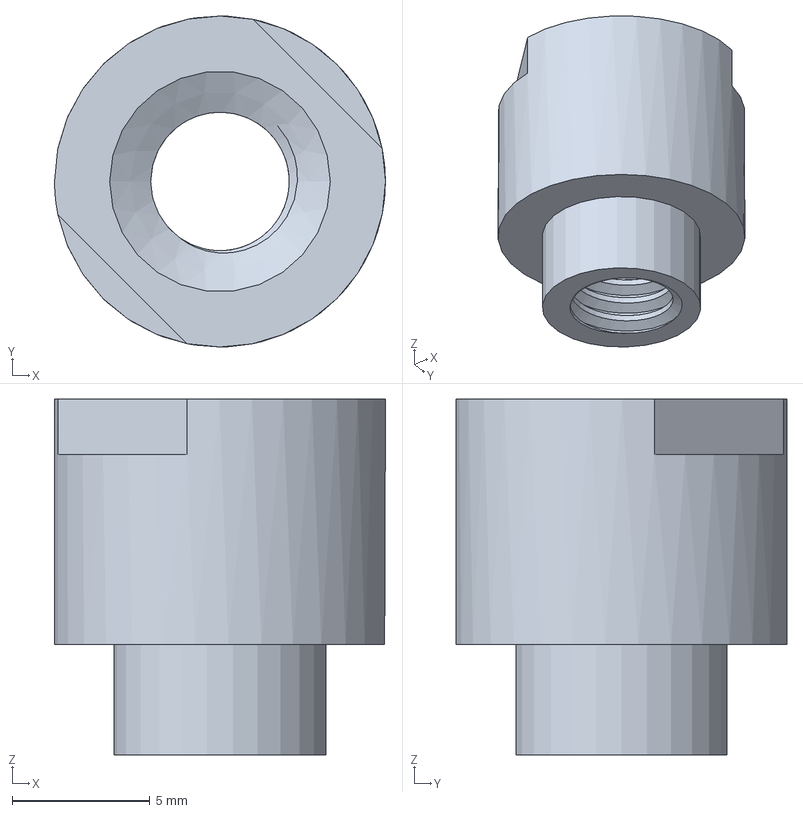
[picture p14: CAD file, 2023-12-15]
AL-DXUv2/prototyping parts/hotend-parts-pipe cap threaded hole.3mf
12.0 x 12.0 x 12.9 mm

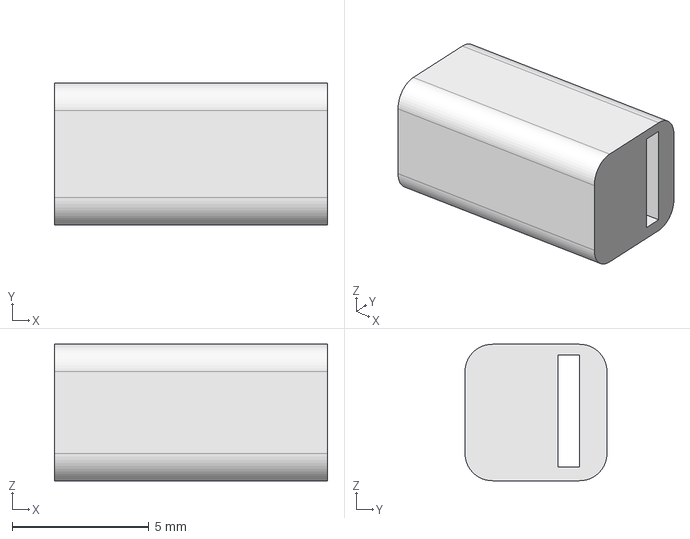
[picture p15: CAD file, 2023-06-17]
AL-DXUv2/prototyping parts/UM2-limit-switch-extension-cap/um2_limit_switch_extension.FCStd
10.0 x 5.20 x 5.00 mm

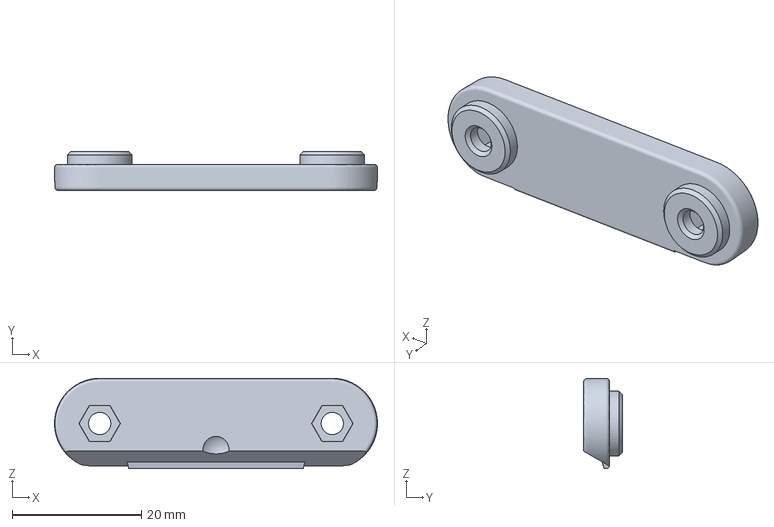
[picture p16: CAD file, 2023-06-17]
AL-DXUv2/UM2 case improvement parts/1156-Zstage-cap-chamfered-clearance/1156-Zshaft-cap-cover.3mf
50.0 x 6.00 x 14.0 mm

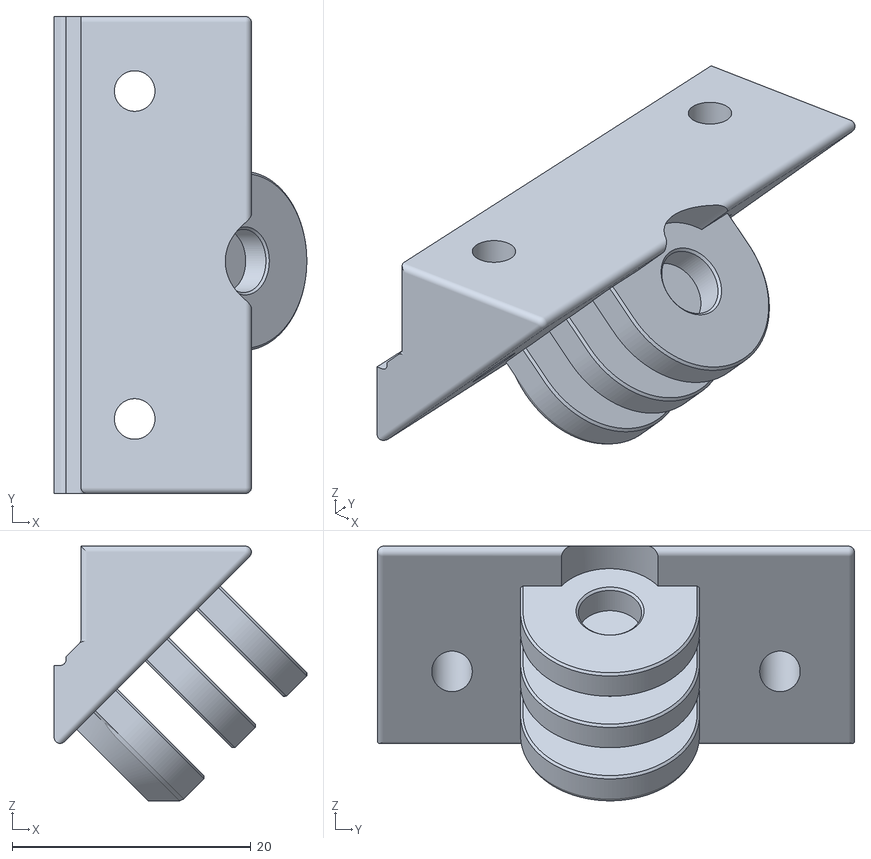
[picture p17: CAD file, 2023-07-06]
AL-DXUv2/UM2 case improvement parts/ESP-EYE-mount/printer-case-mount.stl
21.2 x 40.0 x 21.4

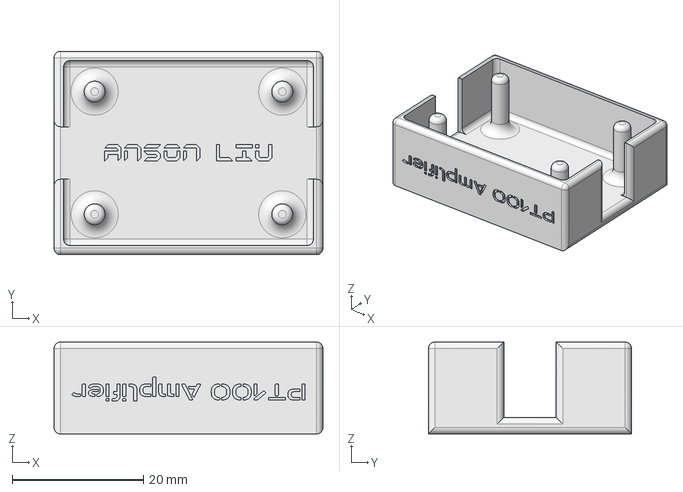
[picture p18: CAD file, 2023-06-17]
AL-DXUv2/UM2 case improvement parts/INA826-PT100-amplifier-board-mount/tl_pt100_amplifier_mount.FCStd
41.0 x 31.0 x 14.0 mm

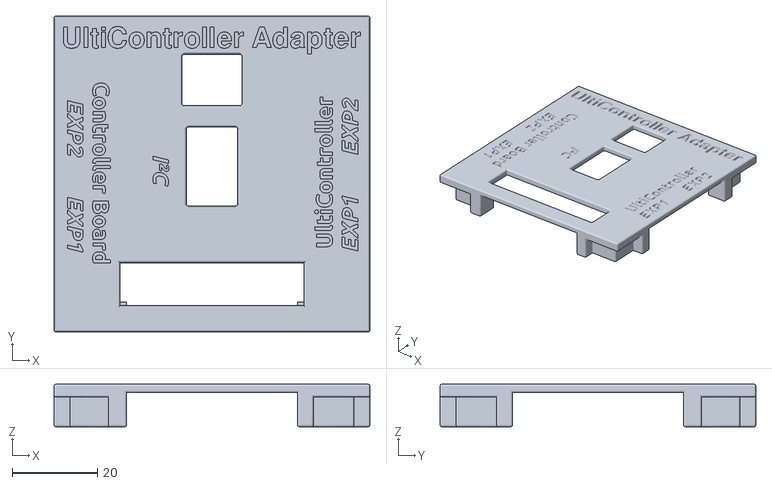
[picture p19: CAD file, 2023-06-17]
AL-DXUv2/UM2 case improvement parts/Ulticontroller-I2C-adapter-board-mount/ulticontroller_i2c_adapter_case_top.stl
74.0 x 74.0 x 10.0

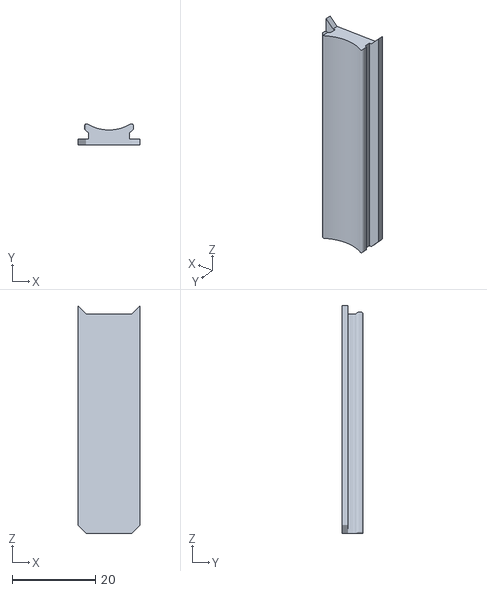
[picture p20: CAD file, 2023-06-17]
AL-DXUv2/UM2 case improvement parts/UM2-case-cable-organizer-trench/cable trench left rear cover 55mm.stl
15.0 x 5.17 x 54.9

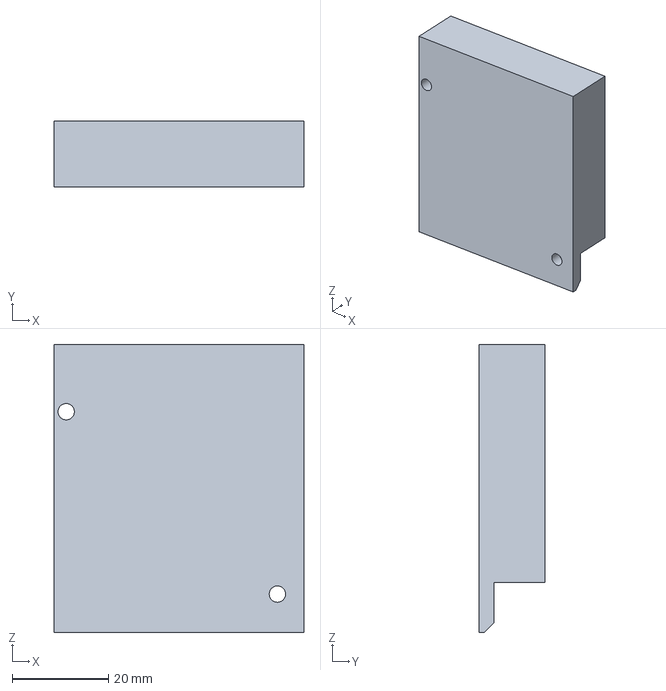
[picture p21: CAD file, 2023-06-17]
AL-DXUv2/UM2 case improvement parts/UM2-case-controller-fan-mount.3mf
52.0 x 13.7 x 60.0 mm

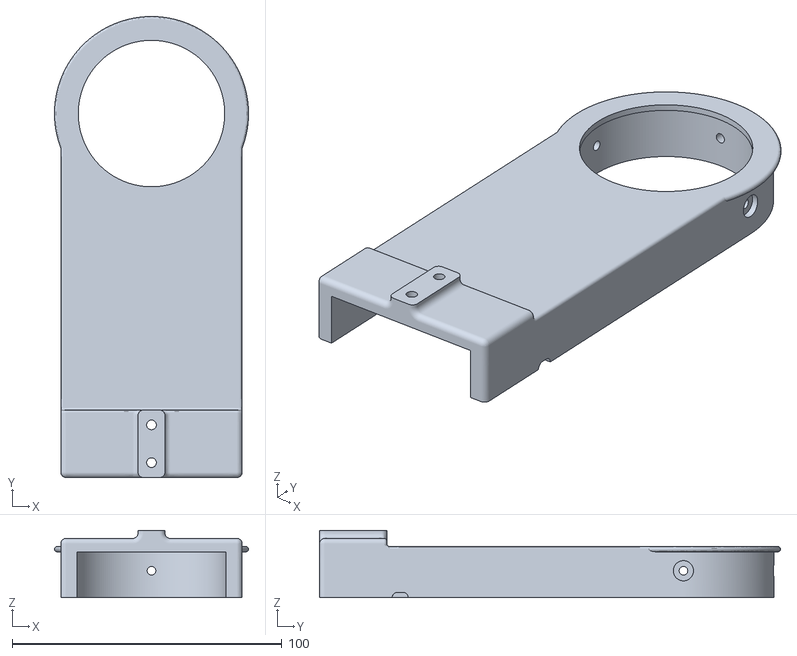
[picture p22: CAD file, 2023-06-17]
AL-DXUv2/UM2 case improvement parts/UM2-case-dual-spool-holder/Mounting_Bracket.stl
72.0 x 171.0 x 25.0

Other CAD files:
AL-DXUv2/UM2 case improvement parts/UM2Plus-feeder-right-mount-retrofit/UM2plus-feeder-retrofit-right.3mf
AL-Hotend Calibration/cube.stl
AL-Hotend Calibration/flat dual calibration/Dual_Extruder_Calibration__Target_B_v2.STL
AL-DXUv2/UM2 case improvement parts/1156-Zstage-cap-chamfered-clearance/1156-zstage-cap-bottom.FCStd
AL-DXUv2/UM2 case improvement parts/ESP-EYE-mount/arm-female.stl
AL-DXUv2/UM2 case improvement parts/ESP-EYE-mount/arm-male.stl
AL-DXUv2/UM2 case improvement parts/ESP-EYE-mount/camera-cover.stl
AL-DXUv2/UM2 case improvement parts/ESP-EYE-mount/camera-mount.stl
AL-DXUv2/UM2 case improvement parts/INA826-PT100-amplifier-board-mount/tl_pt100_amplifier_mount.3mf
AL-DXUv2/UM2 case improvement parts/UM2-case-cable-organizer-trench/cable trench left front lower.stl
AL-DXUv2/UM2 case improvement parts/UM2-case-cable-organizer-trench/cable trench left rear cover 110mm.stl
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

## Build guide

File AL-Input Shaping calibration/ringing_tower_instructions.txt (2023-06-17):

Slice and run ringing_tower.stl model on your printer.
- Slice in vase/spiralize mode. Do not rotate.
- Set high acceleration and speed to show ringing. 
- Change input shaping frequency on each layer with M593. 
- https://marlinfw.org/docs/gcode/M593.html

See which height produces the best results and set the best frequencies. https://www.th3dstudio.com/marlin-input-shaping-calculator/

Premade gcode is created for Ultimaker Original+ size printer with UM2+ upgrades and should work for UM2+. 
- Uses 100mm/s and 10000mm/s^2 for speed and acceleration.
- Uses 220C for nozzle.

For before/after comparison, print the "no_IS" version of the ringing_tower gcode to test the entire ringing tower model at your firmware's set input shaping settings without any change with M593 at each layer. 

My UMO+ with original DXU design input shaping settings:
X freq 45hz
Y freq 40hz
damping factor 0.15

UMO+ with DXUv2 + BLTouch mounted
X freq 41hz
Y freq 36hz
damping factor 0.15

UM2+ stock
X freq 51hz
Y freq 48hz

UM2+ octopus pro
X freq 52hz
Y freq 47hz

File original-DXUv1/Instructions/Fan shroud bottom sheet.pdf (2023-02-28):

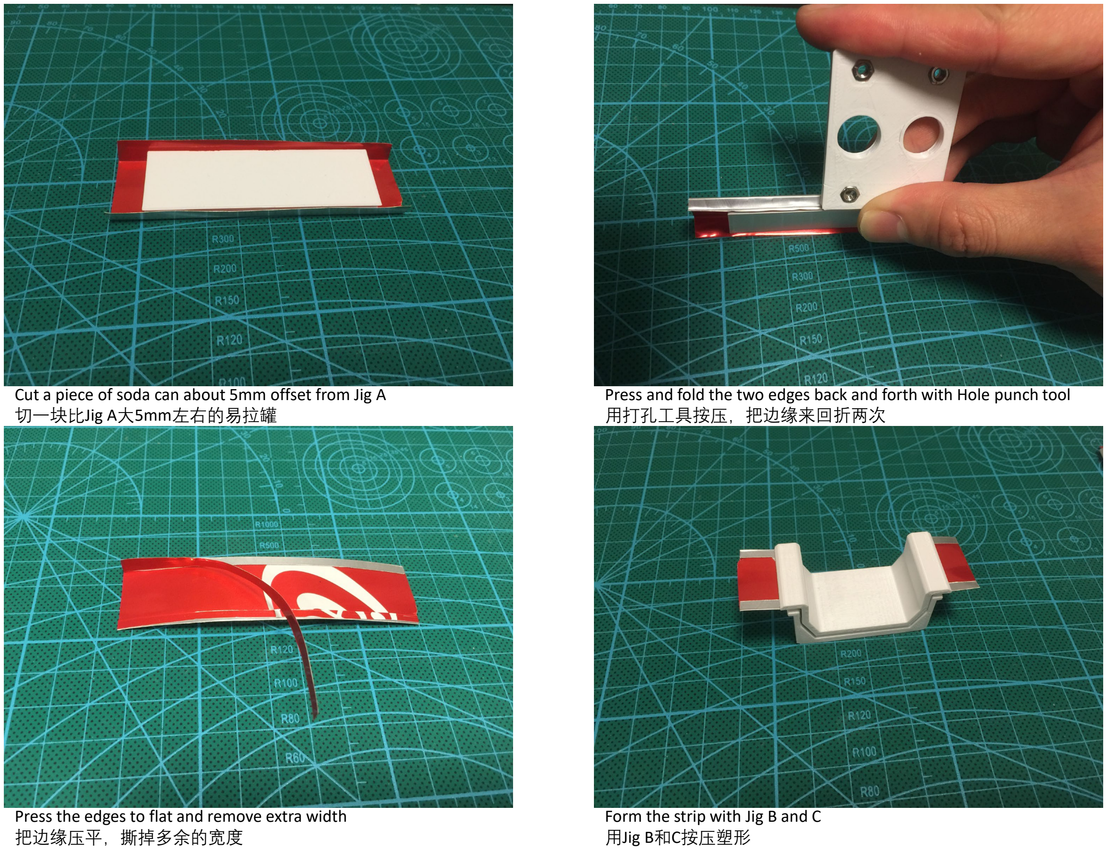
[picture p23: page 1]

Cut a piece of soda can about 5mm offset from Jig A 切一块比Jig A大5mm左右的易拉罐

Press and fold the two edges back and forth with Hole punch tool 用打孔工具按压，把边缘来回折两次

Press the edges to flat and remove extra width 把边缘压平，撕掉多余的宽度

Form the strip with Jig B and C 用Jig B和C按压塑形

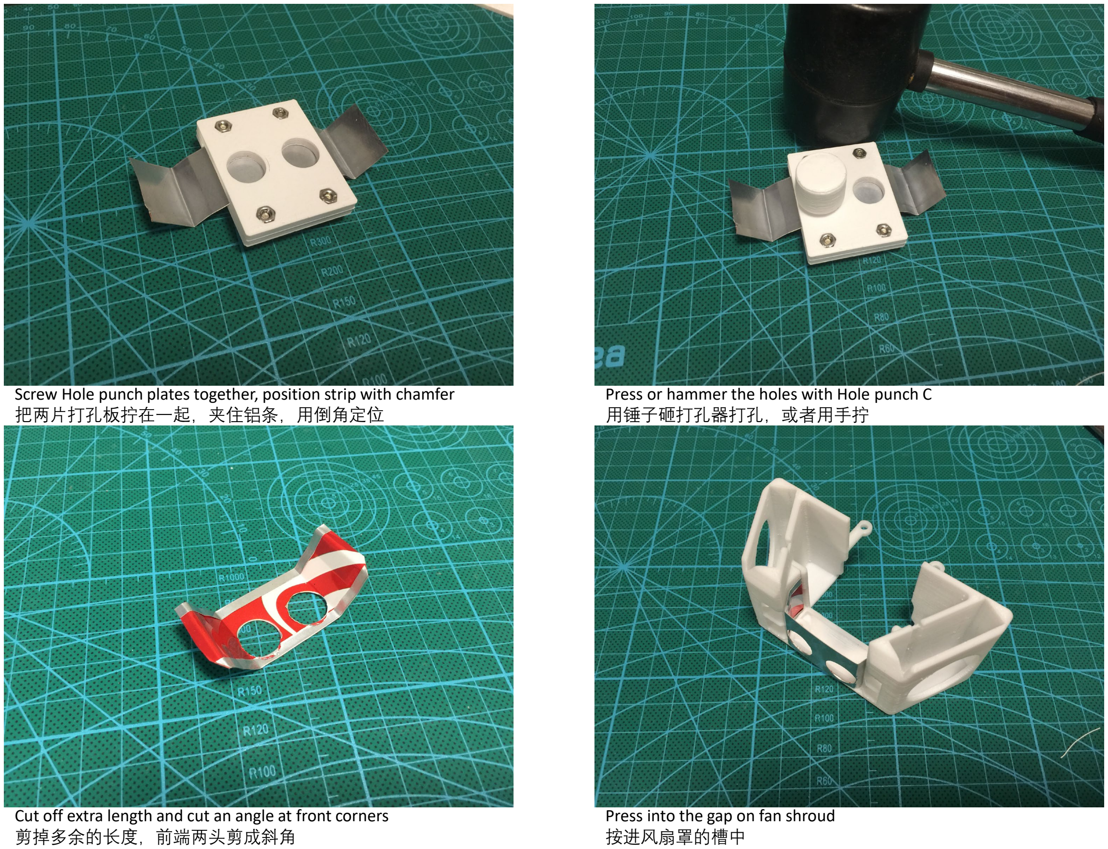
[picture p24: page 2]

Screw Hole punch plates together, position strip with chamfer 把两片打孔板拧在一起，夹住铝条，用倒角定位

Press or hammer the holes with Hole punch C 用锤子砸打孔器打孔，或者用手拧

Cut off extra length and cut an angle at front corners 剪掉多余的长度，前端两头剪成斜角

Press into the gap on fan shroud 按进风扇罩的槽中

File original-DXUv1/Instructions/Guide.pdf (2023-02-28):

DXU 双头升级步骤
1. 组装硬件
a. 购买零件—— 参考物料清单（BOM）
b. 打印部件—— 参考打印推荐设置（Printsettings.xlsx）。需要能够打印高温料的打印机
c. 拆解安装—— 打印头参考组装图纸（Assembly.pdf）。使用 Dockliner.stl 在机身右侧用 3mm 木工钻钻两个眼，用来固定扳手座。
2. 刷新固件
a. 上传固件—— 使用 CURA 上传编译好的固件，标准高度版为 DXU_firmware.hex，加高版为 DXU_Extended_firmware.hex
b. 校准换头位置—— 把打印头上的扳手搬到背部，右头下降的情况下，进入固件调整换头位置
c. 校准双头错位差—— 菜单中粗略设置右头高度，打印 Calibration 文件夹中的 XY_calibration.gcode 以及 Z-calibration.gcode 校准双喷嘴。校 准方法参考 https://magnetic-tool-changer.com/step-6-calibration.html
3. 安装软件
a. 安装 CURA 及插件
安装 CURA3.4 之后，把 Cura resources\3.4 文件夹中的文件复制到 C:\Users\*用户名*\AppData\Roaming\cura\3.4 把 Cura resources\plugins 文件夹中的文件复制到 C:\Program Files\Ultimaker Cura 3.4\plugins
b. 添加相应机型
i. 运行 CURA，添加打印机，选中 DXU，取名 DXU Dual

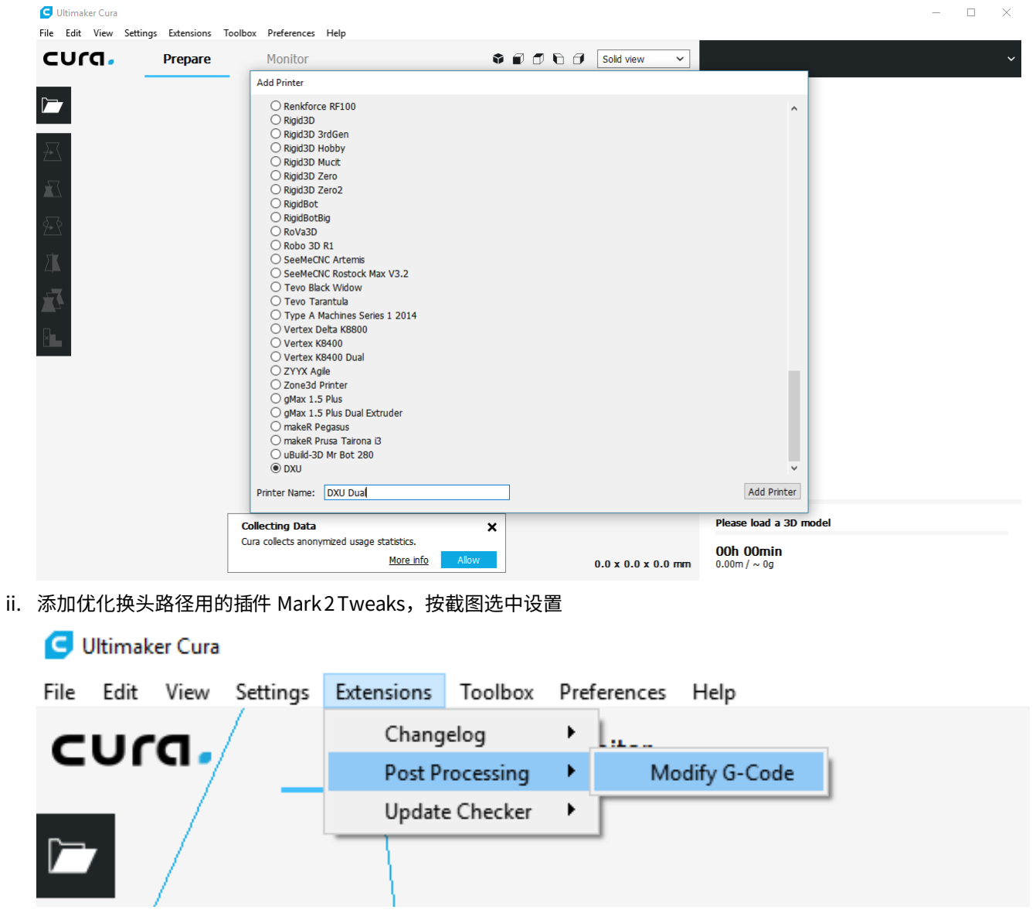
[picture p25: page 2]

ii. 添加优化换头路径用的插件 Mark 2 Tweaks，按截图选中设置

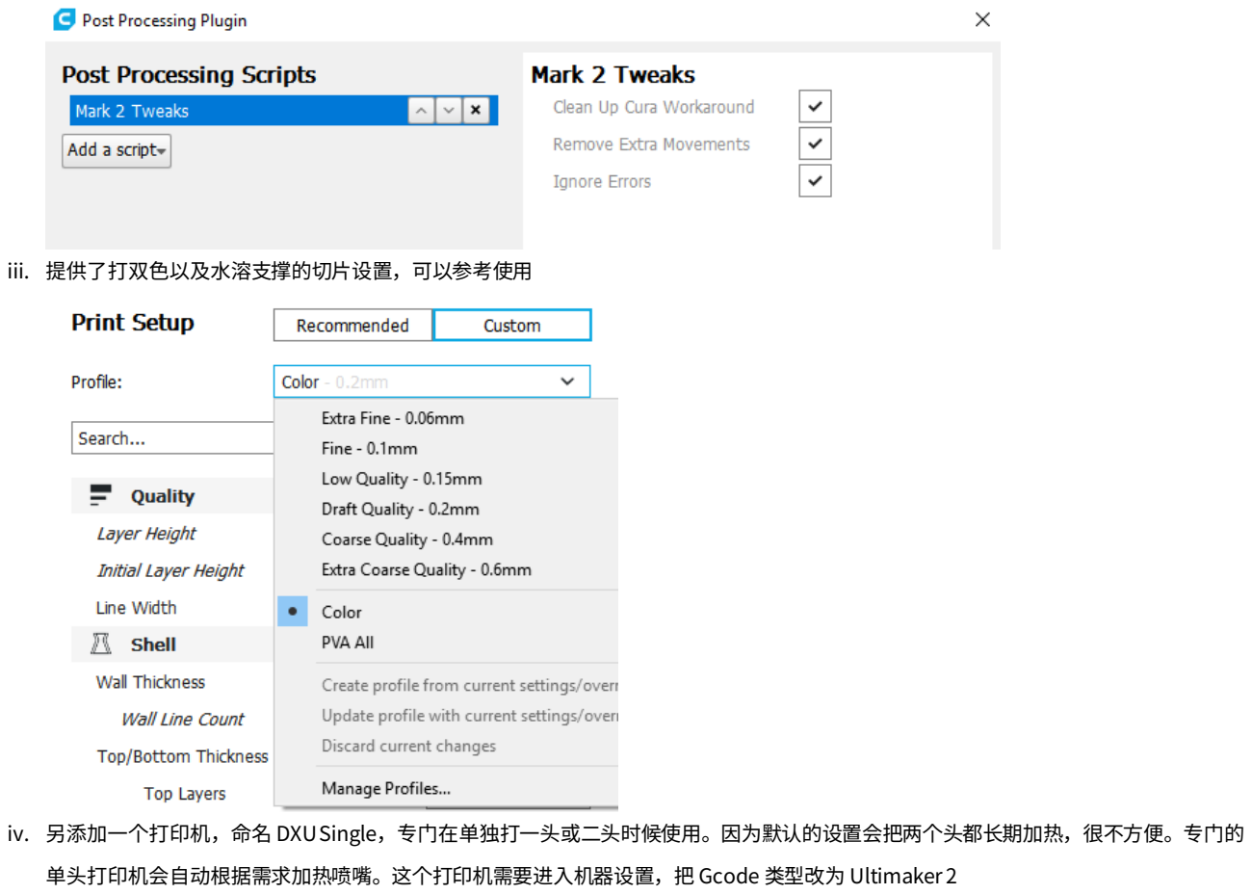
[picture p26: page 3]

iii. 提供了打双色以及水溶支撑的切片设置，可以参考使用

iv. 另添加一个打印机，命名 DXUSingle，专门在单独打一头或二头时候使用。因为默认的设置会把两个头都长期加热，很不方便。专门的 单头打印机会自动根据需求加热喷嘴。这个打印机需要进入机器设置，把 Gcode 类型改为 Ultimaker 2

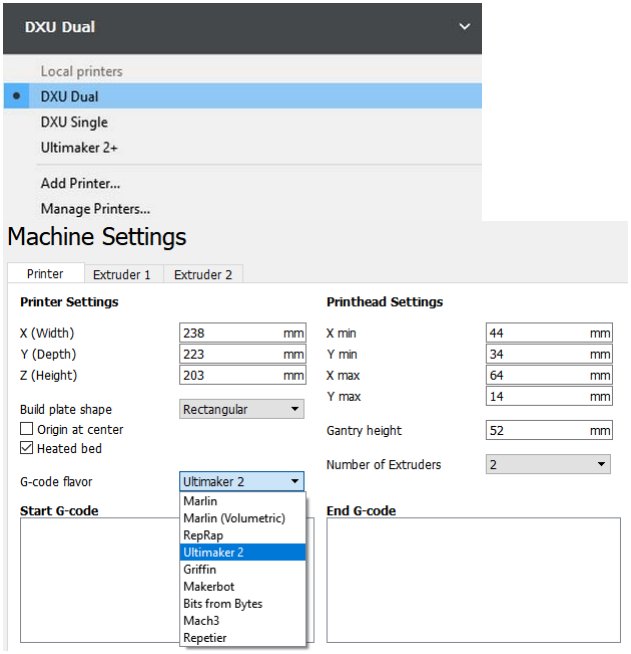
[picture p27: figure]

v. 可打印区域会根据喷嘴使用自动调整

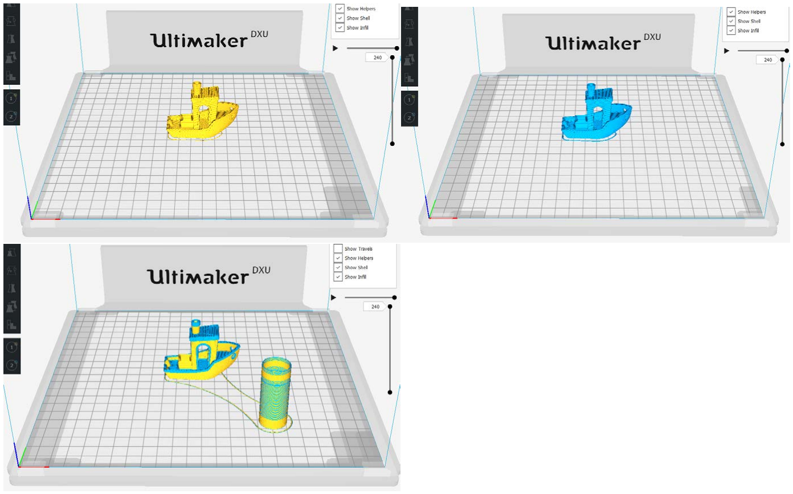
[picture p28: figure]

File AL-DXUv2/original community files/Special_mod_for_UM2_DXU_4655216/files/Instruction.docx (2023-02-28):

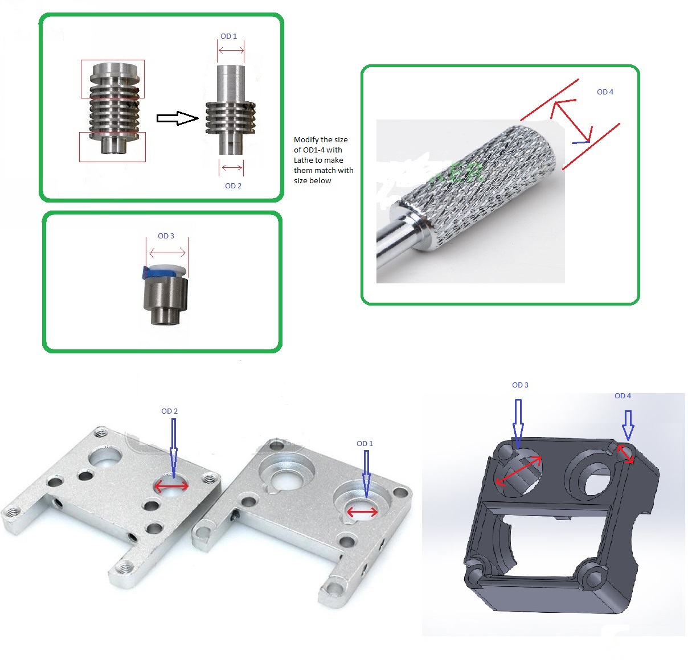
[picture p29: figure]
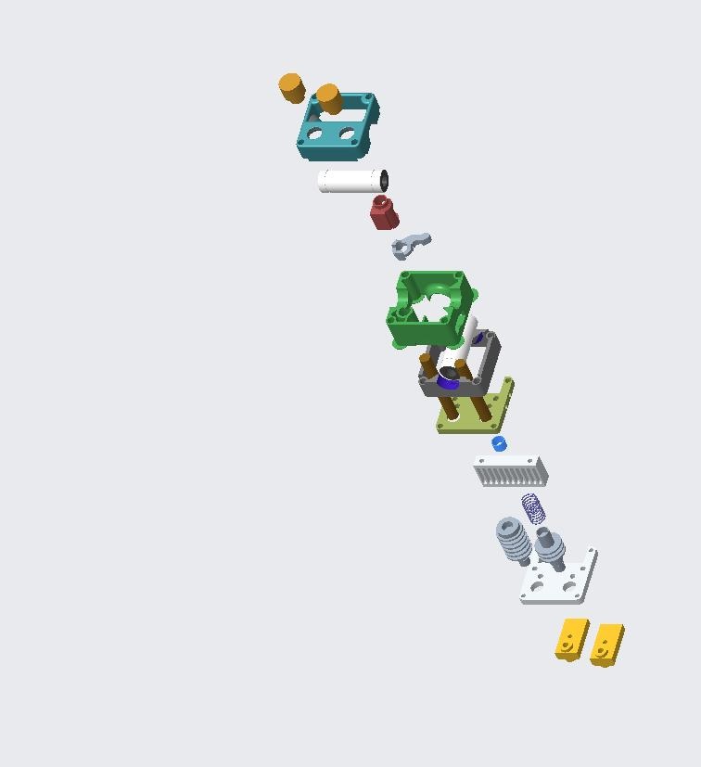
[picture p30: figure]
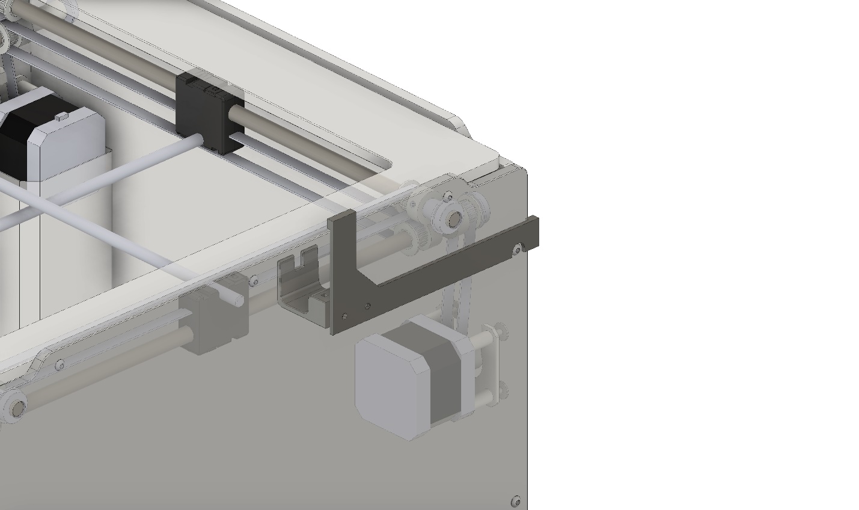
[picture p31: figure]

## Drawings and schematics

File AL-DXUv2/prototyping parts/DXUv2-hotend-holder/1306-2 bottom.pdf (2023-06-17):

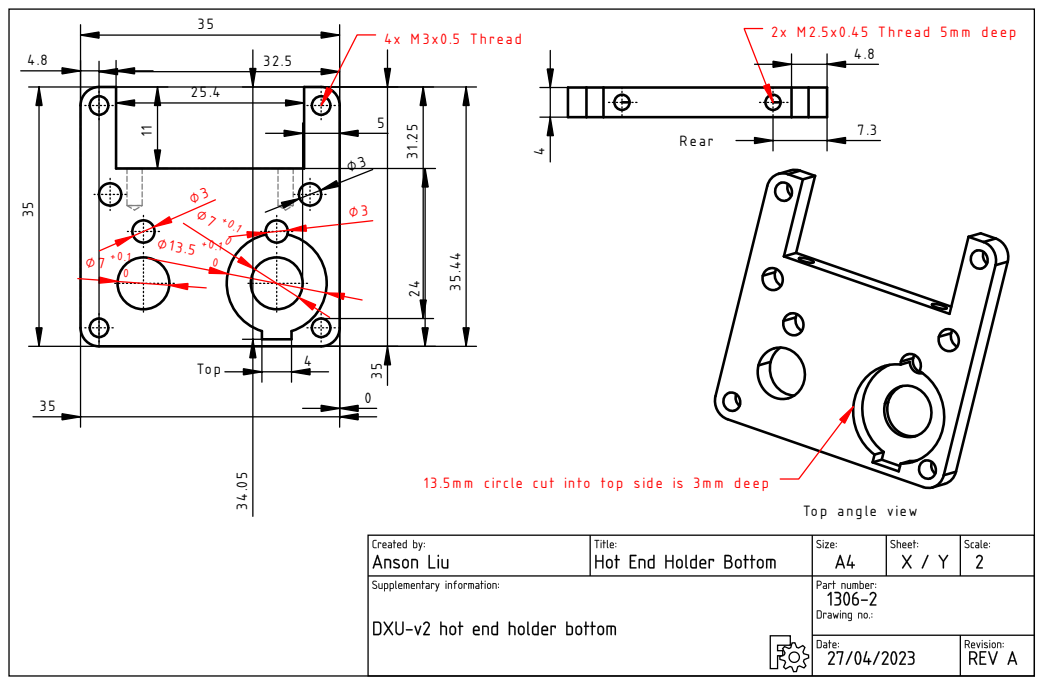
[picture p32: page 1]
Top ⌀ 7 +0.10; m deep 4.87.3 4; Top angle vie w 13.5m m circle cut into top side is 3m m deep

35.44 4 32.5 5 31.25 4x M 3x0.5 T hread 4.8 ⌀ 3 R ear 2x M 2.5x0.45 T hread 5m

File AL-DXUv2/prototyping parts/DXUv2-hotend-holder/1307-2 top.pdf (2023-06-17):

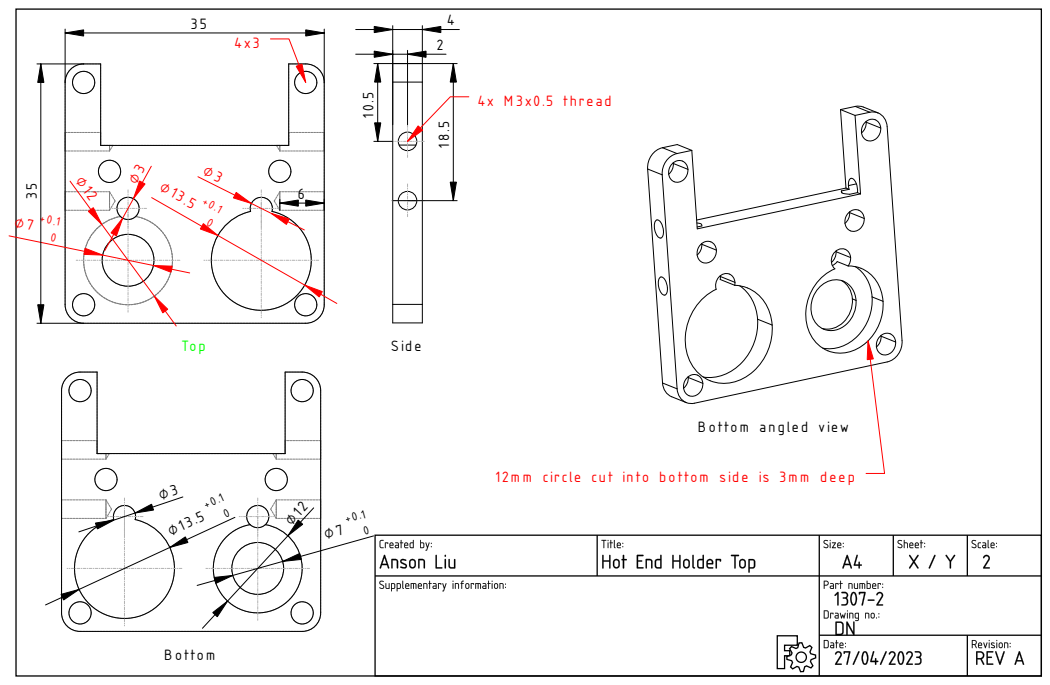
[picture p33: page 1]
B ottom; Top; S ide; 4x M 3x0.5 thread

B ottom angled vie w

12m m circle cut into bottom side is 3m m deep

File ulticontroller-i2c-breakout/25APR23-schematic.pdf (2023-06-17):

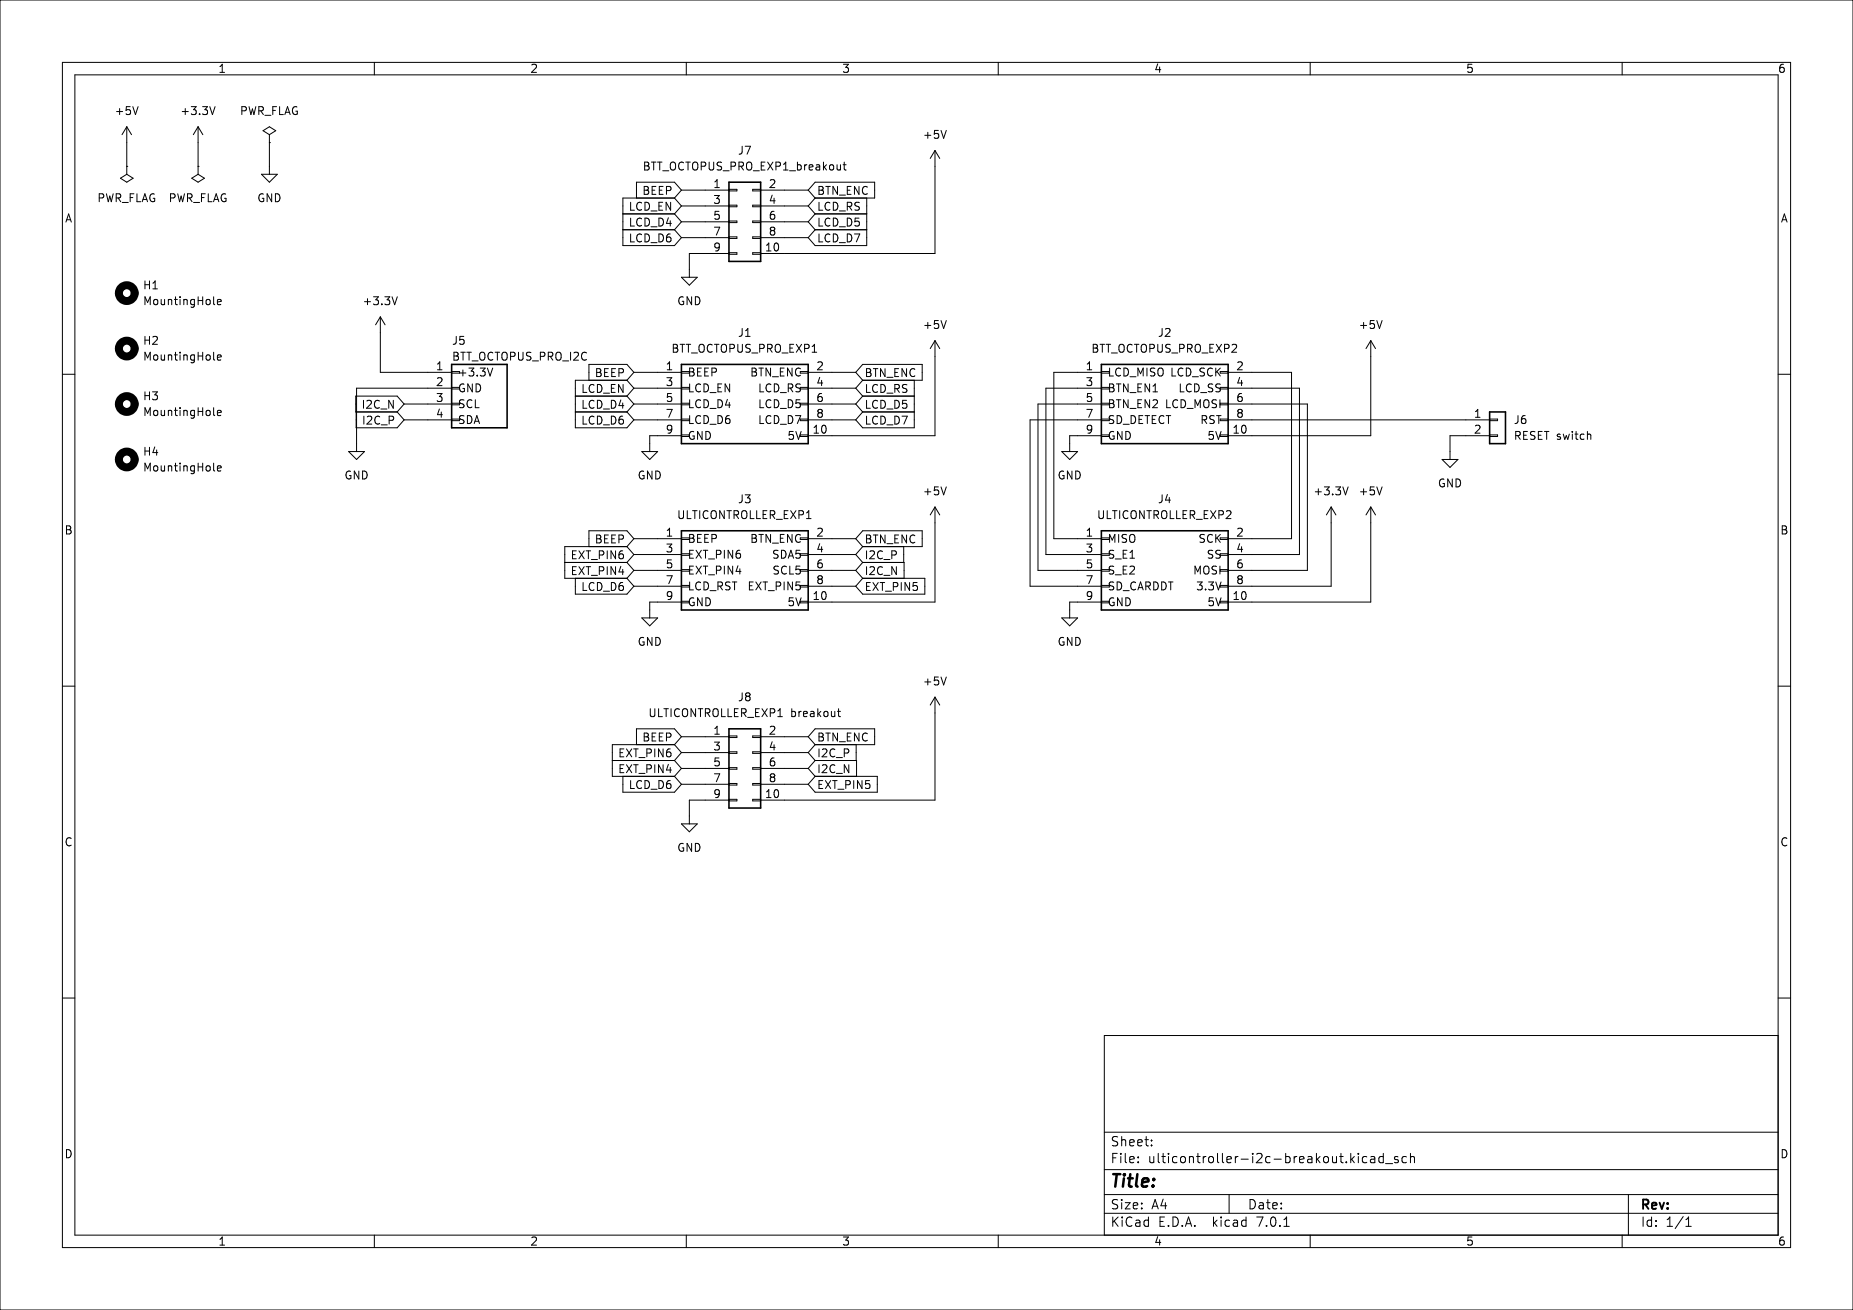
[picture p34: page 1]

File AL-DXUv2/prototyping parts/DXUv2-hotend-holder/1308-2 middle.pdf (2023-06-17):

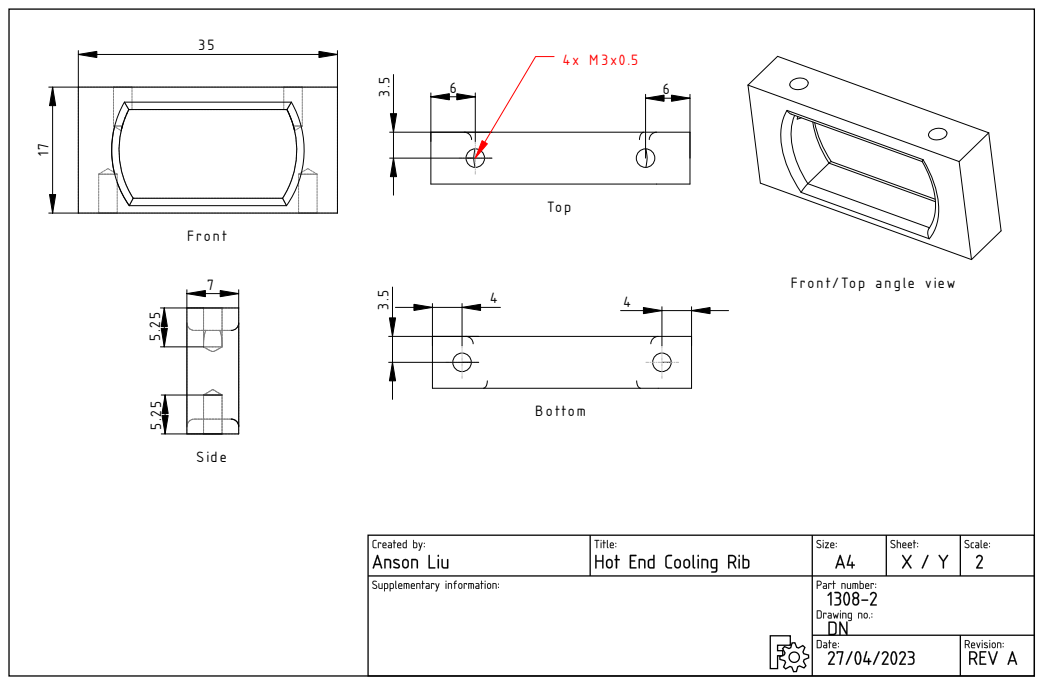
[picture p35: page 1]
Front 35 17; S ide 7 5.25 5.25; Top ³.5; 6 4x M 3x0.5 B ottom ³; Front/ Top angle vie w

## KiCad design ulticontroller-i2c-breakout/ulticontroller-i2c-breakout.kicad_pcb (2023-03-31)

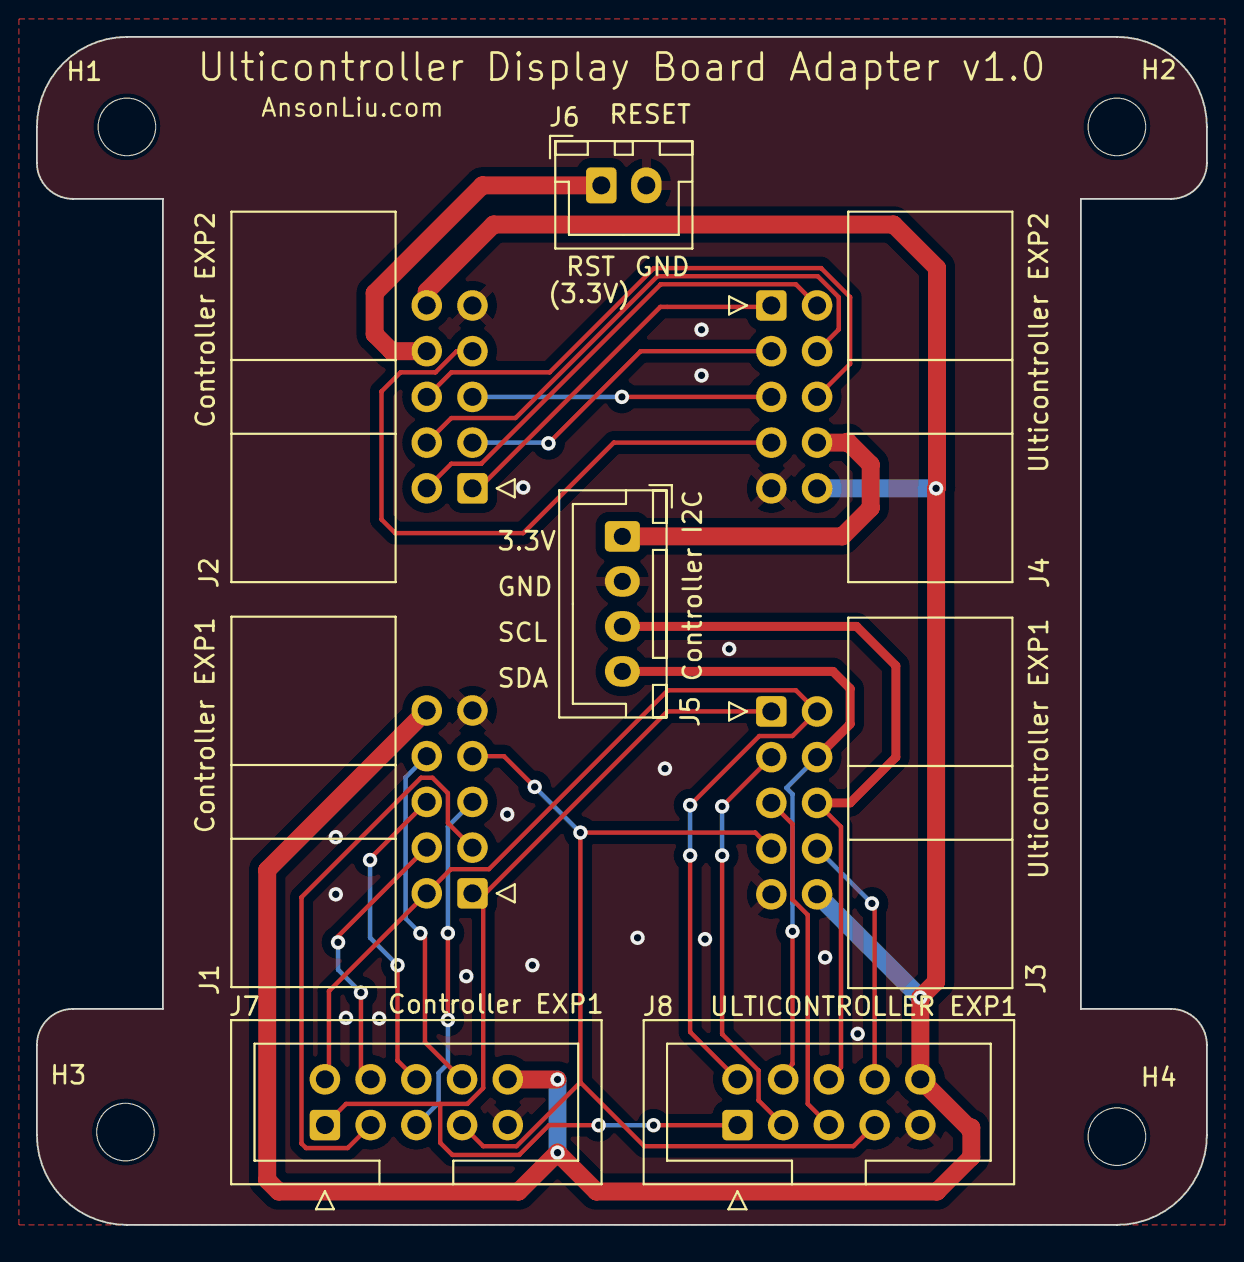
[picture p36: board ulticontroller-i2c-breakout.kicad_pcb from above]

Board: 2 copper layers, 65.0 x 66.0 mm, 12 parts (0 on the bottom side), 24 nets.

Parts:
H1, H2, H3, H4: MountingHole; MountingHole_3.2mm_M3
J1: Controller EXP1; IDC-Header_2x05_P2.54mm_Horizontal
J2: Controller EXP2; IDC-Header_2x05_P2.54mm_Horizontal
J3: Ulticontroller EXP1; IDC-Header_2x05_P2.54mm_Horizontal
J4: Ulticontroller EXP2; IDC-Header_2x05_P2.54mm_Horizontal
J5: Controller I2C; JST_XH_B4B-XH-A_1x04_P2.50mm_Vertical
J6: RESET; JST_XH_B2B-XH-A_1x02_P2.50mm_Vertical
J7: Controller EXP1; IDC-Header_2x05_P2.54mm_Vertical
J8: ULTICONTROLLER EXP1; IDC-Header_2x05_P2.54mm_Vertical

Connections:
+3.3V: J4.8 (3.3V), J5.1 (+3.3V)
+5V: J1.10 (5V), J2.10 (5V), J3.10 (5V), J4.10 (5V), J7.10, J8.10
BEEP: J1.1 (BEEP), J3.1 (BEEP), J7.1, J8.1
BTN_ENC: J1.2 (BTN_ENC), J3.2 (BTN_ENC), J7.2, J8.2
EXT_PIN4: J3.5 (EXT_PIN4), J8.5
EXT_PIN5: J3.8 (EXT_PIN5), J8.8
EXT_PIN6: J3.3 (EXT_PIN6), J8.3
GND: J1.9 (GND), J2.9 (GND), J3.9 (GND), J4.9 (GND), J5.2 (GND), J6.2, J7.9, J8.9
I2C_N: J3.6 (SCL5), J5.3 (SCL), J8.6
I2C_P: J3.4 (SDA5), J5.4 (SDA), J8.4
LCD_D4: J1.5 (LCD_D4), J7.5
LCD_D5: J1.6 (LCD_D5), J7.6
LCD_D6: J1.7 (LCD_D6), J3.7 (LCD_RST), J7.7, J8.7
LCD_D7: J1.8 (LCD_D7), J7.8
LCD_EN: J1.3 (LCD_EN), J7.3
LCD_RS: J1.4 (LCD_RS), J7.4
unnamed: J2.1 (LCD_MISO), J4.1 (MISO)
unnamed: J2.2 (LCD_SCK), J4.2 (SCK)
unnamed: J2.3 (BTN_EN1), J4.3 (S_E1)
unnamed: J2.4 (LCD_SS), J4.4 (SS)
unnamed: J2.5 (BTN_EN2), J4.5 (S_E2)
unnamed: J2.6 (LCD_MOSI), J4.6 (MOSI)
unnamed: J2.7 (SD_DETECT), J4.7 (SD_CARDDT)
unnamed: J2.8 (RST), J6.1

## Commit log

2022-12-28 initial stable changes
    [BOM_aliexpress.xlsx, dock-UMO-exact.stl, dock-UMO-thicker-frame-tolerance.stl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]
2023-01-08 reorganized and added input shaping calibration
    [BOM_aliexpress.xlsx, dock-UMO-exact.stl, dock-UMO-thicker-frame-tolerance.stl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]
2023-02-28 add DXUv2 design
    [Print_Settings.xlsx, base1.STL, base2.STL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]
2023-02-28 rename to DXUv1
    [BOM_aliexpress.xlsx, dock-UMO-exact.stl, dock-UMO-thicker-frame-tolerance.stl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]
2023-02-28 rearrange files for DXUv2
    [01 Housing Front.stl, 02 Housing Back.stl, 03 Fan Shroud 3510.stl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]
2023-03-20 rename input shaping tower
    [ringing_tower_prusaslicer_0.25nozzle.3mf]
2023-03-31 add breakout board
    [ulticontroller-i2c-breakout.kicad_pcb, ulticontroller-i2c-breakout.kicad_sch]
2023-06-17 add DXUv2 files
    [1156-Zshaft-cap-cover.3mf, 1156-zstage-cap-bottom.FCStd, UM2-case-controller-board-mount-cura.3mf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]
2023-06-17 add spool holder
    [Filament_Guide.stl, Mounting_Bracket.stl, Pin.stl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]
2023-07-06 add ESP-EYE mount
    [arm-female.stl, arm-male.stl, camera-cover.stl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]
2023-07-16 add Cura configs
    [Dual_Extruder_Calibration_Target_A_v1-1.STL, Dual_Extruder_Calibration__Target_B_v2.STL, cube.stl]
2023-08-07 Update cura default printer settings
2023-12-15 Added extruders for Cura profile and zip file
    [hotend-parts-heater block threaded hole.3mf, hotend-parts-pipe cap threaded hole.3mf, hotend-parts-pipe heatsink assembly w_ through hole.3mf]
2024-02-17 Enable relative extrusion
